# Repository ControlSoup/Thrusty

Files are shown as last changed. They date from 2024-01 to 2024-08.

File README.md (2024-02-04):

# How to Use

Assuming you have the required permissions to access this file. Here is how to clone and run the various projects in this file.

### Generate an ssh key

For a guide on how to generate an ssh key to clone this repo, see ->
[Github ssh keygen](https://docs.github.com/en/authentication/connecting-to-github-with-ssh/generating-a-new-ssh-key-and-adding-it-to-the-ssh-agent)

### Clone the repo

Use the ssh key on this repo and find a nice place in your file structure for it to be stored (Git folder, documents ect)

After you find that, open that path in a terminal.

Once your terminal is open, perform:
```bash
git clone [pasted ssh key form github]
```

### Install requirments and folder as a package

Once the repo is cloned, navigate to its file path, and perform the following command.

```
python3 -m pip install .
```

the "." denotes that you want to install the current folder (with setup.py)

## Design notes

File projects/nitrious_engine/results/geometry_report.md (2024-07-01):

==================== Geometry Report ====================
Chamber Area [in^2] = 5.94
Chamber Diameter [in] = 2.75
Chamber Length [in] = 6.0
Chamber Volume [in^3] = 37.38
Contraction Ratio [-] = 5.62
Exit Area [in^2] = 3.269
Exit Diameter [in] = 2.04
Exit Half Angle [rad] = 0.268
Exit Length [in] = 1.603
Expansion Ratio [-] = 3.093
Half Angle Losses [-] = 0.982
Lstar [in] = 35.37
Throat Area [in^2] = 1.057
Throat Diameter [in] = 1.16

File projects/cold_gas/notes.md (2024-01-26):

# Requirements:
- Model the thrust fluid conditions of a cold gas thruster
- Affordable at the hobby scale
- Model Supply requirements and run time for a given thruster setup
- Allow different gas storage parameters such as:
	- Fluid Medium
	- Pressure
	- Temperature
- Bonus Research Questions I want to answer:
	- Why Isentropic for choked flow conditions?
	- Can you make a vehicle that can fly for 5-10s from only cold gas propulsion?

# Sources:
- [Rocket Propulsion Elements #9](obsidian://open?vault=sattva&file=Papers%2FRocket%20Propulsion%2FTextbooks%2FRocket%20Propulsion%20Elements%209.pdf)

# Modeling Force!

Force in a nozzle is a product of the momentum of something exiting it. In the case of propulsion systems often these are very small particles of gas, at very high velocities. For a converging diverging nozzle I will use the following symbolic notation in the represented form:

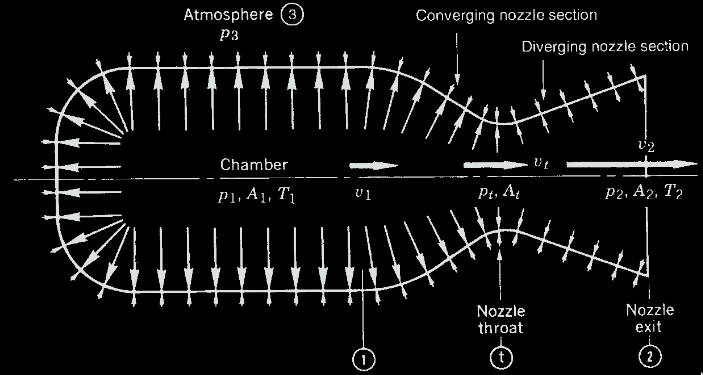
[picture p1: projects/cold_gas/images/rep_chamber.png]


The equation for thrust form the conditions through this system is :
$$\huge F = \dot{m}v_2 + (p_2-p_3)A_2$$

The derivation of this equation is from the Control Volume Approach from refs 2-3 and 2-4 in - [Rocket Propulsion Elements #9](obsidian://open?vault=sattva&file=Papers%2FRocket%20Propulsion%2FTextbooks%2FRocket%20Propulsion%20Elements%209.pdf).

The Chamber conditions are fairly easily defined from the source or tube attached to the system $p_1,A_1,T_1$. Seal Level atmospheric pressure is a great assumption for this project ($p_3$), so really... its just about finding the values for $\dot{m}$,  $v_2$ and $p_2$ given $A_2$.
##### Complete Thrust Equation

Note:
	the symbol $\kappa$ refers to a real gas constant, see : [[WIKI_Heat_capacity_ratio.pdf]]
	in some equations you will see $\gamma$ instead of $\kappa$

To capture the various gas effects going on, we need an equation that allows modification of the chamber geometry, working medium ect. The following equation can be used to perform trades on these various parameters.

Eq 3-29 from [Rocket Propulsion Elements #9](obsidian://open?vault=sattva&file=Papers%2FRocket%20Propulsion%2FTextbooks%2FRocket%20Propulsion%20Elements%209.pdf).
$$\huge F = A_tp_1\sqrt{\frac{2\kappa^2}{\kappa-1}\space\space\space\space(\frac{2}{\kappa+1})^\frac{\kappa+1}{\kappa-1}\space\space\space\space[1-\frac{p_2}{p_1}^\frac{\kappa-1}{\kappa}]} + (p_2 - p_3)A_2$$

This is an awesome equation for an initial design, however there will be need to be able to look at test data and directly compare with predictions. For this the thrust coefficient can be used.

##### Thrust Coefficient

These equations are essentially the same thing as the full thrust equation just shifting things around to make more direct comparisons with data.

Eq 3-30 from [Rocket Propulsion Elements #9](obsidian://open?vault=sattva&file=Papers%2FRocket%20Propulsion%2FTextbooks%2FRocket%20Propulsion%20Elements%209.pdf).
$$\huge C_F = \sqrt{\frac{2\kappa^2}{\kappa-1}\space\space\space\space(\frac{2}{\kappa+1})^\frac{\kappa+1}{\kappa-1}\space\space\space\space[1-\frac{p_2}{p_1}^\frac{\kappa-1}{\kappa}]} + \frac{A_2(p_2-p_3)}{A_tp_1} $$
and combining this with this full thrust equation gives us the final easy to compare formula for test data:

Eq 3-31 from [Rocket Propulsion Elements #9](obsidian://open?vault=sattva&file=Papers%2FRocket%20Propulsion%2FTextbooks%2FRocket%20Propulsion%20Elements%209.pdf)
$$\huge F = C_FA_tp_1$$
or for our use
$$\huge C_F = \frac{F}{A_tp_1}$$

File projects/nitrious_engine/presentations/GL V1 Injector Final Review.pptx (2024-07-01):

## Gaslighter V1 Engine FINAL REVIEW

Designer: Karl Kanmaz
Systems Engineer: Joe Wilson

## GL V1 Ideal System Specs

- Chamber Pressure = 150 psi
- Throat Diameter = 1.33 in
- Bulk Chamber Temp = 1937 F
- L* = 30 in
- MR = 1.6
- Area Ratio = 2.25
- Mass flow = 1.68 lbm/s
Max Thrust = 267.2 lbs

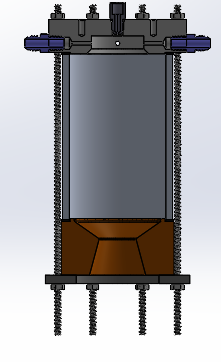
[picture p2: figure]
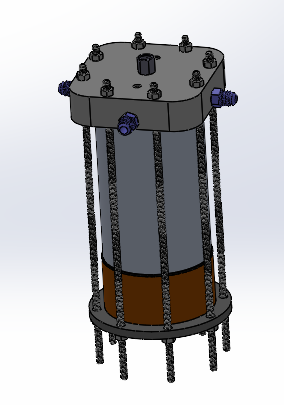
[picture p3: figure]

## Design

Injector
Material: 6061 Aluminum

Chamber
Material: 6061 T6 Tube
- Adjustable

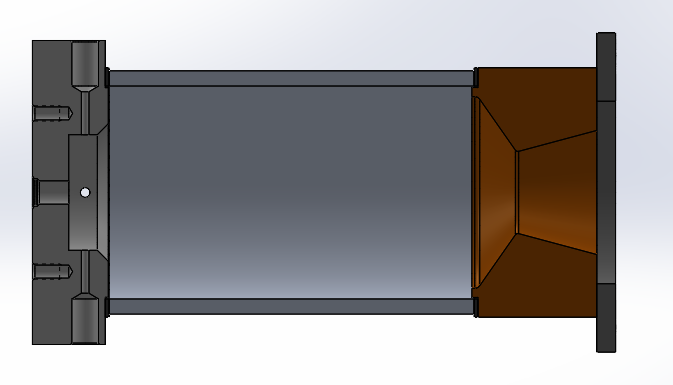
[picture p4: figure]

Clamp Plate
Material: Mild Steel

Graphite Gasket

Throat-Nozzle
Material: 360 Brass

## Pressure Ladder

Mdot_fuel = 0.65 lbm/s (0.29 kg/s)
V_tank = 0.011 m^3
Ullage % = 10%
Mass_fuel_max = 8 kg
Max Burn Time = 28 s

Injector Orifice 2X
Dp = 31.3 psi
P = 150 psi
⌀ 0.155”

Fuel Tank
187 psi

F-V-052

Injector

Chamber
150 psi

Outlet Pipe
Dp = 2.6 psi
P = 184.3 psi
Length = 4.9 ft
⌀ 0.44”
Relative Roughness= 0.0015

Branch Pipe 2X
Dp = 2.2 psi
P = 182.1 psi
Length = 10”
⌀ 0.375”
Roughness = …

Sump
Dp = 0
P = 187 psi
⌀ 0.5”
Cd = 0.65

Sump

Ball Valve - 052
Dp = 0.2 psi
P = 186.8 psi
Cv = 11.7

## Load - Cell Threads

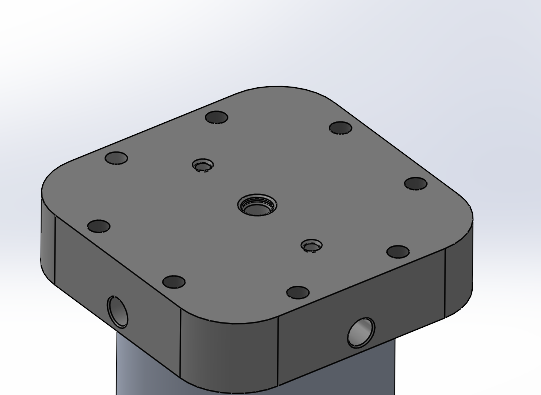
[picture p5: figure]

2X ¼” - 28 Thread
Length = 0.5”
Athread = PI*dm*Le / 3
Fsu = 30 ksi
FOS = 2
Pallowed = 2000 lbf (per thread)
- Aluminum threads may wear after many uses, be prepared to insert helicoil replacement

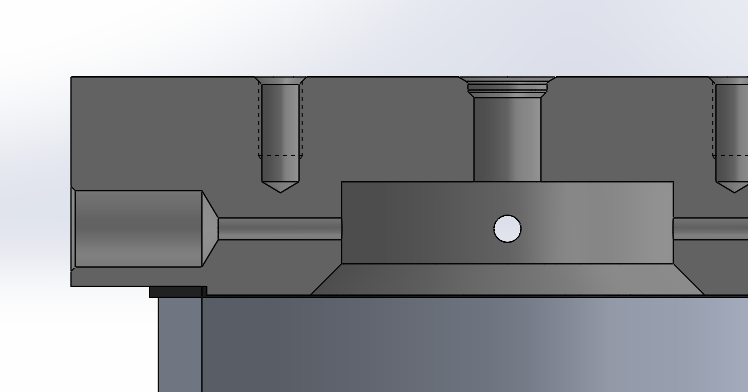
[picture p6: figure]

## Chamber Pressure Stress

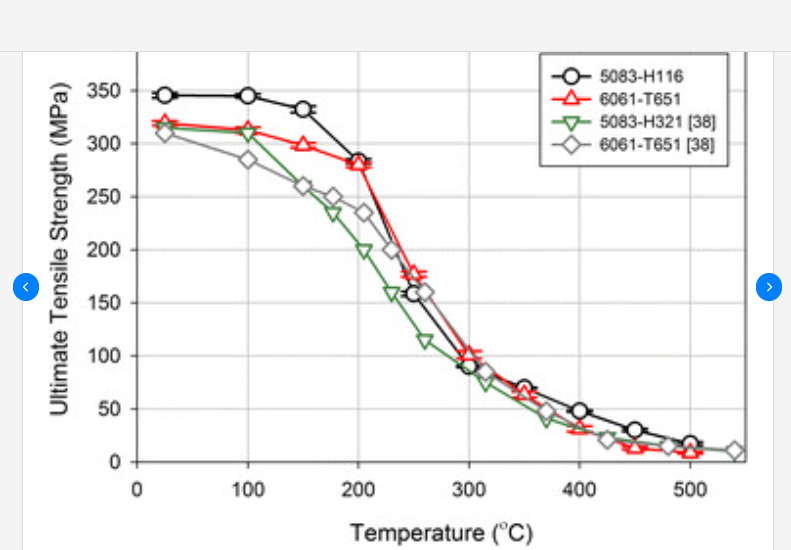
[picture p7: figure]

Hoop Stress = Pr/t
= (150 psi) * (1.75”) / (0.25”)
= 1050 psi [7 MPa]
- FOS_ult = 2
- Temp should be limited to approx. 400 Celsius ( 752 F)

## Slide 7

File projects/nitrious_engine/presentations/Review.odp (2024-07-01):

## Gaslighter V1 Engine FINAL REVIEW

Karl Kanmaz, Joe Wilson

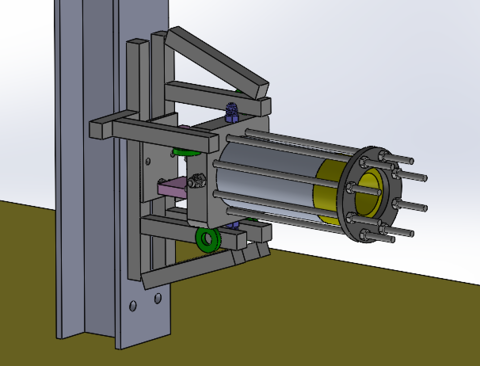
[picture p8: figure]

## Engine

- Chamber pressure chosen to keep fuel runtank < 200psia
- Engine mdot limited by fuel runtank pressures and volume (0.5gal/5s)
- Mixture ratio chosen to keep ideal chamber temps 10% over melting (1730F)
  - This is an conservative choise, based on combustion efficency expectations
  Design decisions on this motor are intended to provide
  an easy onramp to liquid propulsion instead of optimizing performance.

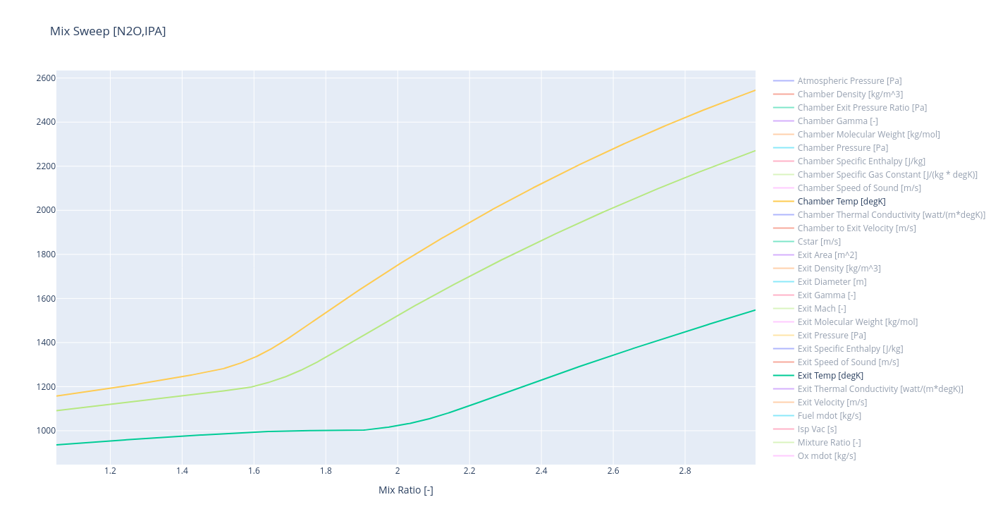
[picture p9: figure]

## Propellant

- Fuel: 99% Ipa
- Oxidizer: N2O (Automotive)
- Combustion properties from CEA
  Propellants chosen for their ease of use and avaliblity, at the cost of performance.
  Additional complexity is added by the use of a high vapor pressure oxidizer, this was perfered over the challanges of cryogenics for a small hobby project.

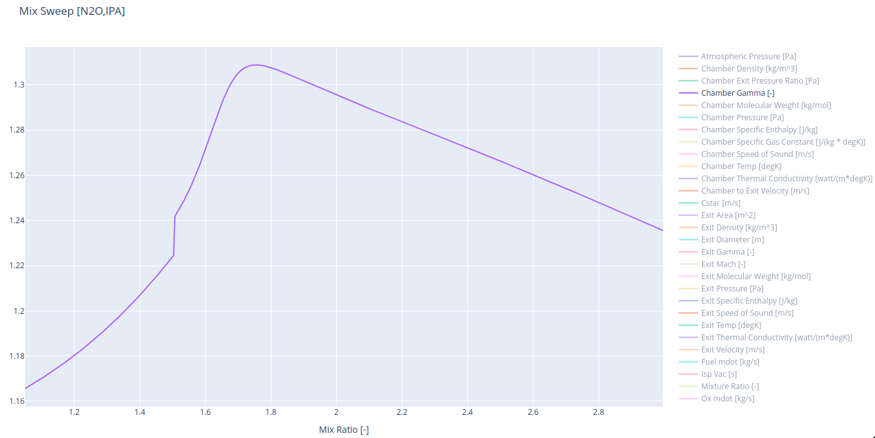
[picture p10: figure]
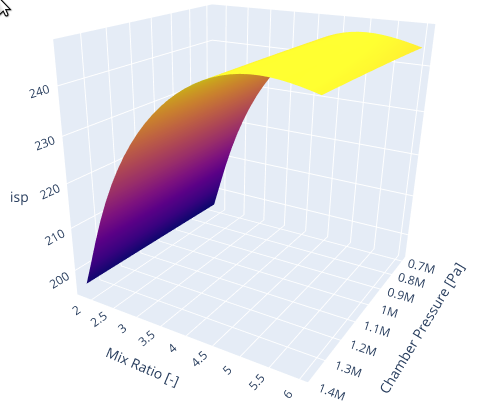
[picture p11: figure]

## GL V1 Ideal System Specs

- Chamber Pressure = 150 psi
- Throat Diameter = 1.33 in
- Bulk Chamber Temp = 1730 F
- L* = 30 in
- MR = 1.06
- Area Ratio = 2.25
- Mass flow = 1.68 lbm/s

Ideal Thrust = 267.2 lbs

## Design

Injector

Material: 6061 Aluminum

- Center OX orifice

- 2X fuel orifice (90 deg to OX orifice)

Chamber
Material: 6061 T6 Tube

ID: 2.75”

Length: 6”

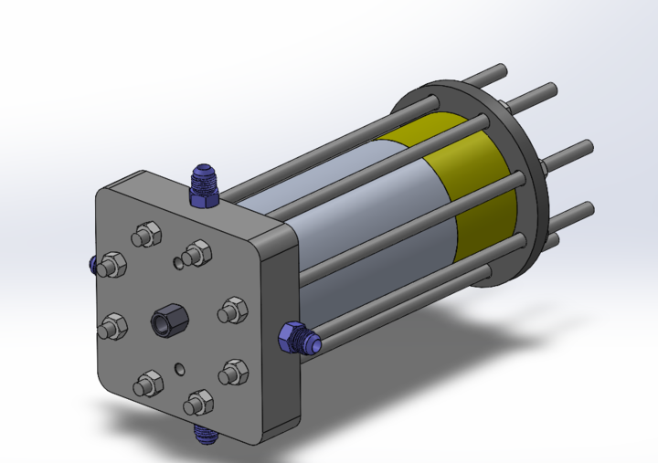
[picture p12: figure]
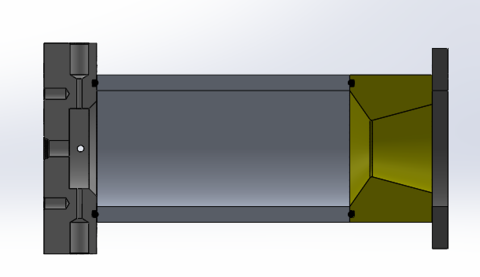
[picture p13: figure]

Clamp Plate

Material: Mild Steel

High Temp O-ring

Throat-Nozzle

Material: 360 Brass

## Heat Sink Modeling

- Assumes 100% Combustion Efficiency, and perfectly caloric products
- Throat temp = Chamber stagnation temperature
- Diffusivity chosen based by median flame temp (293K -> 1250K)
- Copper C360 (Brass) chosen to balance cost, melting temp and conductivity
- Heat transfer done with FDM discrete and rk4 integration

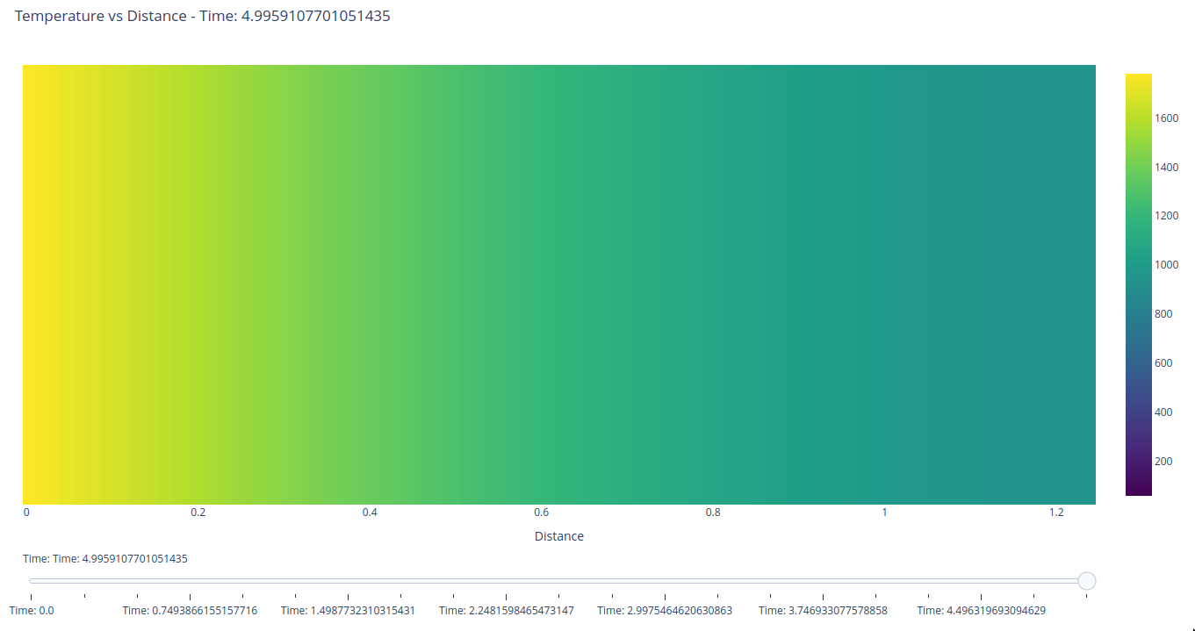
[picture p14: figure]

  780K Adiabatic Outer Wall Temp

Ambient Properties (https://www.matweb.com/search/DataSheet.aspx?MatGUID=bae961d2d6ed497a9096986641162def)

  Frontiers of Solidifcation (MPMD 2016)

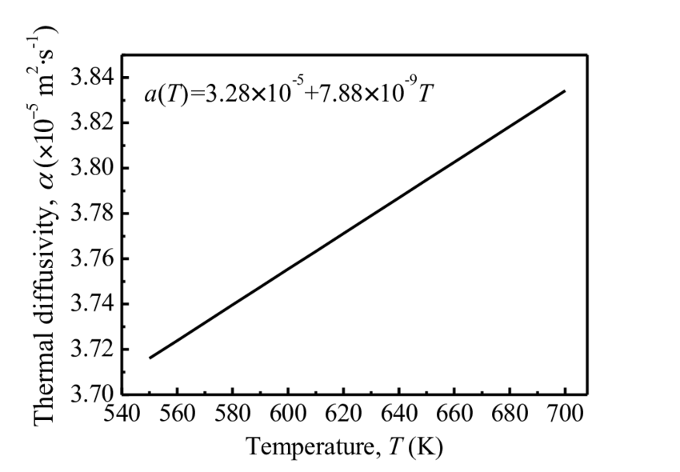
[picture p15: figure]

  Ambient Diffusivity (293K) = ~3.59e-5 [m2/s] Frontier Model Diffusivity(293K) = ~3.51e-5 [m2/s] Frontier Model Diffusivity(771K) = ~3.89e-5 [m2/s]
  Calc is likely conservative, but this demonstrates worst case conditions, and drives starting mixture ratio selection.
  Melting temp 1160K (0.141in)!

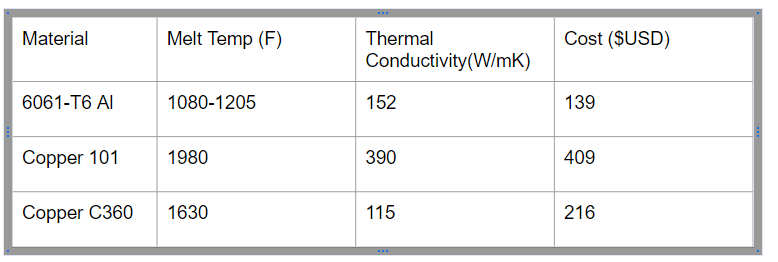
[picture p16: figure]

  1244K [FROM CEA]

## Throat Errosion

  Based on conservative heat sink modeling, throat erosion is likely.
  Effects of this:
  - Chamber pressure reduction
  - Exit Ratio decreases inverse with Exit Pressure and proportional to Exit velocity
  - Slight Chamber temperature reduction
  - Increased mdot from both injectors
  - For small erosion thrust increases, until exit velocity compromises mdot increase
  Risks:
  - Reduced injector stiffness (instability, or combustion gas up the feedline)
  - Loss of engine performance (lower isp, transition to under expansion and decreased exit velocity)
  Even with max expected errosion during a 5s burn, thrust loss is minimal. Injector stiffness risk will be accepted, and mitigated with an intial lower duration burn to access erosion

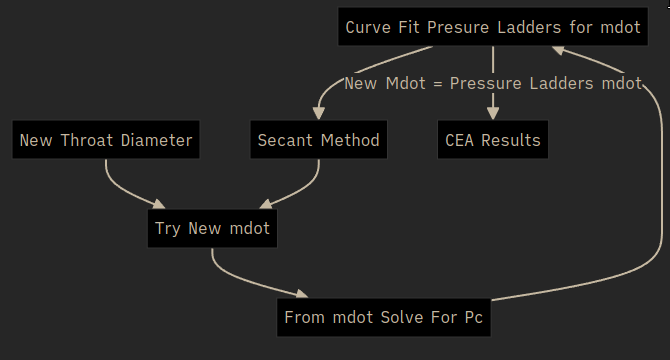
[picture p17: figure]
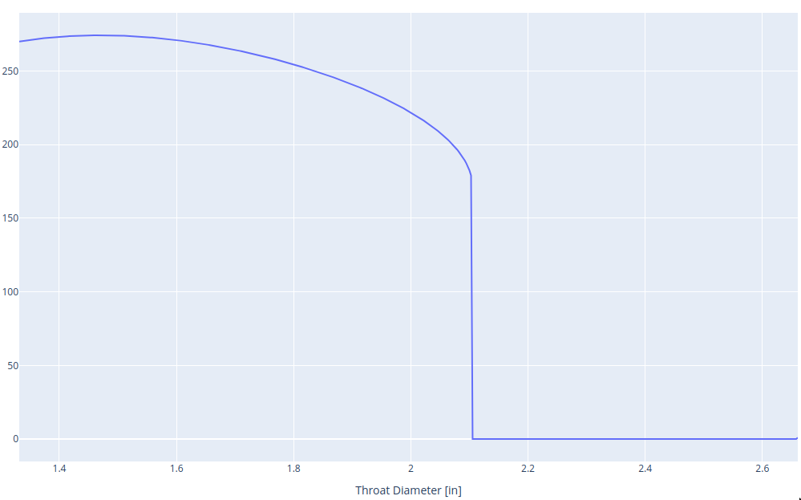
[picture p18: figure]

  Expansion = Unity
  Thrust

## Test P&ID / Instrumentation

  Risk Profile:
  - 2 Fault tolerant during manual operations
  - 1 Fault tolerant to loss of GSE
  - 0 Fault tolerant to engine loss
  Nitrous:
  - Nitrous outlet 20lbm + high flow siphon valve
  - Pressure / Temp at all major locations
  - Redundant purge checks to mitigate leakage flowing into fuel system if checked off
  - 4 x calibrated load cells to measure mass usage against injector mdot
  IPA:
  - IPA temperature considered ideally constant, only ullage pressure and injector fluid state are measured
  - 4 x calibrated load cells to measure mass usage against injector mdot
  Purge:
  - Limits moisture (from icing in Nos leakage or combustion products)
  - Acts as a small gas damper during startup (startup timing tbd)
  Chamber:
  - Chamber pt with thermal standoff
  - Chamber temperatures although low enough to measure with a K-type TC where not installed due to possibilities of increased chamber temps in the future
  - 3 x Skin temperature sensors on injector wall, chamber wall and throat location
  If budget allowed normally open valves , a remote pressurant isolation, and a separate volume for purge gas would have been desirable from a test stand perspective.

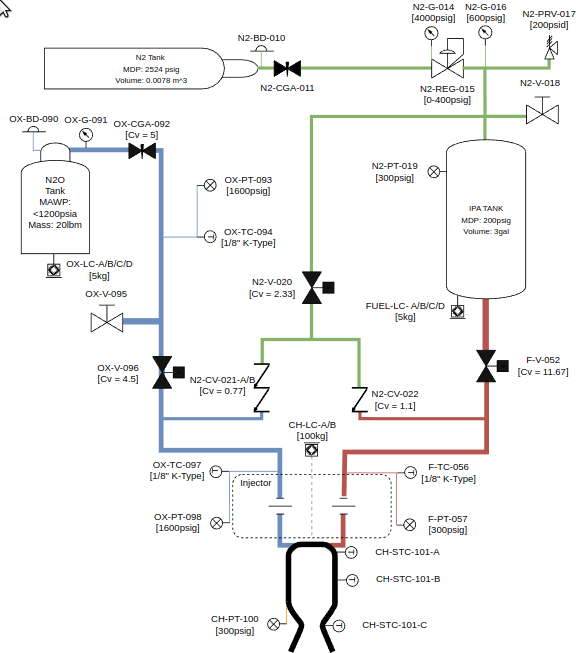
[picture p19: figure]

## Fuel Feed Pressure Ladder

Fuel Tank

187 psi

F-V-052

Injector

Chamber

150 psi

Mdot_fuel = 0.65 lbm/s (0.29 kg/s)

V_tank = 0.011 m^3

Ullage % = 10%

Mass_fuel_max = 8 kg

Max Burn Time = 28 s

Injector Orifice 2X

Dp = 31.3 psi

P = 150 psi

⌀ 0.155”

Branch Pipe 2X

Dp = 2.2 psi

P = 182.1 psi

Length = 10”

⌀ 0.375”

Roughness = …

Sump

Sump

Dp = 0

P = 187 psi

⌀ 0.5”

Cd = 0.65

Needle Valve - 052

Dp = 0.2 psi

P = 186.8 psi

Cv = 11.7

Outlet Pipe

Dp = 2.6 psi

P = 184.3 psi

Length = 4.9 ft

⌀ 0.44”

Relative Roughness= 0.0015

## Purge Sizing

- Control Mass Flow by choking upstream of feedlines this ensures down stream conditions do not effect purge mass flow-rate until critical conditions are met
- Ensure a minimum of 3 x volume exchanges based onNASA Lessons Learned (https://llis.nasa.gov/lesson/851) (For hydrogen but few sources exist for nitrous oxide / IPA)

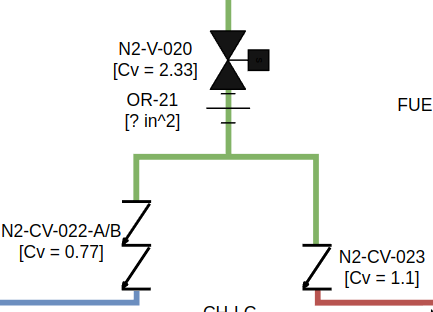
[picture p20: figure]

## Fuel Tank

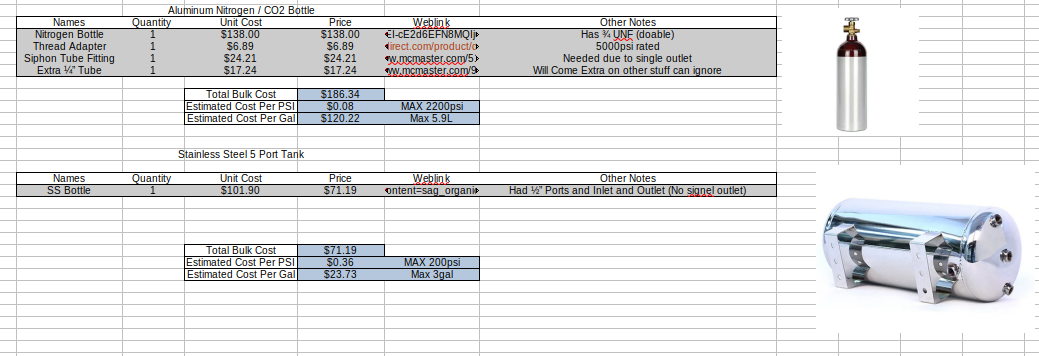
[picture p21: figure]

  Fuel Tank was chosen purley on cost and for lack of fabrication, for higher chamber pressures tapping the bottom of the nitrogen bottle, buying a 3/4” UNF fitting and proofing the assembly per B31.3 would be very cost effective

## DESIGN ANALYSIS

## Chamber Pressure Hoop Stress


Hoop Stress = Pr/t

= (150 psi) * (1.375”) / (0.375”)

= 550 psi [4 Mpa]

- Temp should be limited to approx. 400 Celsius (752 F) for chamber structural capability

## Seals

- O ring Diameter = 1/8” (0.139” Exact)
- O-ring maximum rated temperature = 450 F
  Pressure Separation Force = 1800 lbf
  Threaded Rods: 5/16” – 18 x 1 ft
  Joint Separation min. pre-load = 900 lbf
  Tie-rod min torque = 7.2 in-lbs

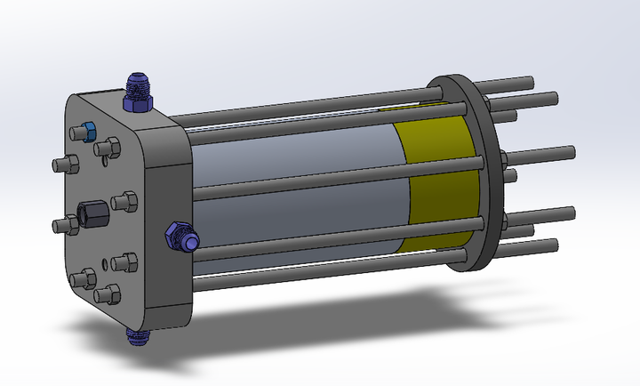
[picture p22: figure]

Separation Pressure

## Chamber Thermal Expansion

- Aluminum chamber will experience thermal expansion of 0.020” per every 100F heating
- Steel tie rods will experience same elongation and therefore increased tension during hot fire  Tie Rod Total Tension =

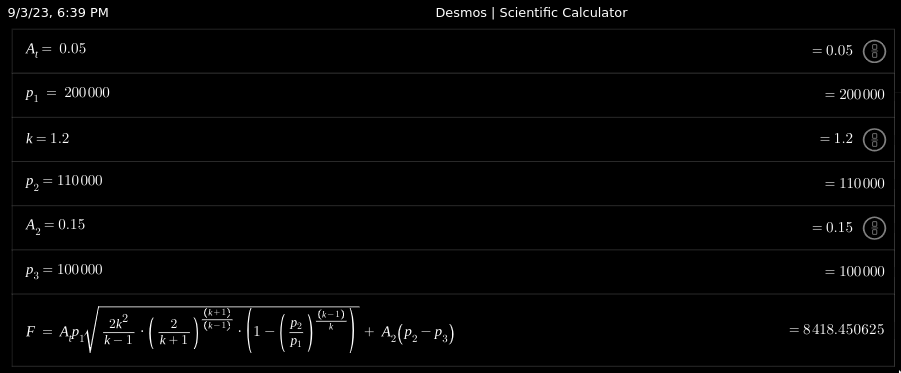
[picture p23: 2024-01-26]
projects/cold_gas/images/RPE_EQ-3-28_desmos.png

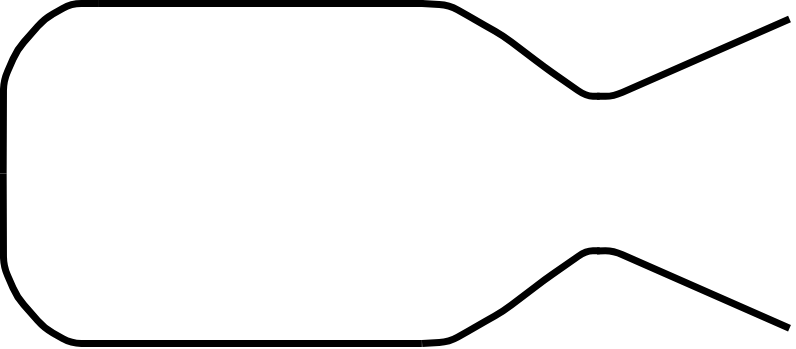
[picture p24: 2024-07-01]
projects/nitrious_engine/diagrams/engine.png

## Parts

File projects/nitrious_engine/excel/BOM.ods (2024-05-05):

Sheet: Global BOM
 |  | GSE BOM
Names | Quantity | Unit Cost | Price | Weblink | Other Notes | Ordered
Pressure Relief (300psig) | 2 | $29.74 | $59.48 | https://www.mcmaster.com/9889K19-9889K162/ | -
NOS Pts | 3 | $34.69 | $104.07 | https://www.amazon.com/FUSCH-Transducer-Connector-Stainless-Transmitter/dp/B0CRQT7VFJ | -
Fuel + Chamber Pts | 3 | $25.00 | $75.00 | https://www.amazon.com/Transducer-Stainless-Transmitter-Automobile-Motorcycle/dp/B09FXBHW9F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 | -
In Fluid Tcs | 3 | $30.44 | $91.32 | https://www.mcmaster.com/39095K64/ | -
TC Extension Wire | 1 | $28.94 | $28.94 | https://www.amazon.com/K-Type-Thermocouple-Wire-Solid-Insulation/dp/B074DKPJRL | -
Engine Load Cells | 2 | $25.00 | $50.00 | https://www.amazon.com/YZC-516C-Tension-Compression-Weight-batching/dp/B0BG9TH1S8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 | 100kg
N2 Regulator | 1 | $36.99 | $36.99 | https://www.amazon.com/Nitrogen-Regulator-Delivery-Pressure-Connection/dp/B09FXSDTFY | -
N2 Tank | 1 | $138.95 | $138.95 | https://www.amazon.com/Nitrogen-CGA580-Valve-Fresh-Certification/dp/B00CA31IMY | -
Fuel Tank | 1 | $127.00 | $127.00 | https://www.amazon.com/Kegco-I22-580-Nitrogen-Pressure-Aluminum/dp/B0037B3BLE | -
1000psi Valves | 3 | $17.26 | $51.78 | https://www.mcmaster.com/4112T23/ | -
Check Valves | 2 | $22.20 | $44.40 | https://www.mcmaster.com/7775K52/ | -
NOS Feed Valve | 1 | $109.98 | $109.98 | https://www.amazon.com/dp/B0CL6NX9V2/ref=twister_B0CL76SKJP?_encoding=UTF8&psc=1 | - | X
Purge Valve | 1 | $59.98 | $59.98 | https://www.amazon.com/U-S-Solid-Pressure-Solenoid-Valve/dp/B0BSNCWW34?hvadid=680323326402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 | -
Fuel Feed Valve | 1 | $84.98 | $84.98 | https://www.amazon.com/U-S-Solid-Pressure-Solenoid-Valve/dp/B0BSNHJ4WQ?hvadid=680323326402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 | -
NOS Tank | 1 | $495.97 | $495.97 | https://nitrousoutlet.com/cart | -
Fitting, Tube ect | 1 | $300.00 | $300.00 |  | Need to Add Detail
Tube Cutter | 1 | $15.99 | $15.99 | https://www.amazon.com/Libraton-Tubing-Deburring-Aluminum-Stainless/dp/B09J2JY1Q6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 | - | X
Tube Bender | 1 | $31.99 | $31.99 | https://www.amazon.com/VEVOR-Pipe-Tube-Bender-Manual/dp/B0C4F6BWDX | - | X
Tube Flare | 1 | $153.75 | $153.75 | https://www.aircraftspruce.com/catalog/topages/flaringtools2.php | - | X
Tank Load Cells | 8 | $1.75 | $13.98 | https://www.amazon.com/WWZMDiB-Amplifier-HX711-Displacement-Acceleration/dp/B0BLNQVY2X | 5kg
 |  | GSE Total | $2,074.55
 |  | Ignitor Bom
Names | Quantity | Unit Cost | Price | Weblink | Other Notes
Holder | 1 | $10.23 | $10.23 | https://www.mcmaster.com/9149K24/ | Thicker Wall for Snug Fit
Adapter | 1 | $6.28 | $6.28 | https://www.mcmaster.com/50785K614/ | -
Cap | 1 | $2.96 | $2.96 | https://www.mcmaster.com/50785K164/ | - |  | Total | $2,113.49
 | Ignitor Total | 2 | $38.94
 |  | DAQ
Names | Quantity | Unit Cost | Price | Weblink | Other Notes
TC Board | 1 | $52.95 | $52.95 | https://www.amazon.com/K-Type-Thermocouple-Breakout-MAX31855-200%C2%B0C/dp/B0B8B4CHDW?hvadid=652512145088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 | Comes With 8 Tcs
Power Supply | 1 | $23.99 | $23.99 | https://www.amazon.com/ALITOVE-Universal-Regulated-Switching-Transformer/dp/B078RTV9C4?hvadid=242168461154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 | 30A Max
Plug and Fuse | 1 | $10.00 | $10.00 | https://www.amazon.com/ASHATA-Rocker-Switch-Adapter-Printer/dp/B085VSS1F2?hvadid=647168045727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 | 15A Fuse
Valve Switches | 3 | $17.99 | $6.55 | https://www.tti.com/content/ttiinc/en/apps/part-detail.html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 | Spring Return Switches
ESTOP | 1 | $9.99 | $9.99 | https://www.amazon.com/Baomain-Emergency-Switch-Button-Weatherproof/dp/B00NTT91Y0 | STOP IT ALL
Diagnosis | 1 | $7.58 | $7.58 | https://www.amazon.com/Multimeter-Probe-Binding-Banana-Panel/dp/B0113IH0IW?hvadid=459486921002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 | Multi Meter Jacks
Cover Switches | 1 | $10.71 | $10.71 | https://www.amazon.com/Nilight-90014E-Rocker-Toggle-Warranty/dp/B07QKFD7Z7?hvadid=362768105905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 | Red Cover
TC Bulkheads | 4 | $6.50 | $25.98 | https://www.amazon.com/dp/B08BKTFJKX?s=industrial&sp_csd=d2lkZ2V0TmFtZT1zcF9kZXRhaWw | TC Bulkheads
 |  | COMS
Names | Quantity | Unit Cost | Price | Weblink | Other Notes
Walkie Talkie | 1 | 20.88 | 20.88 | https://www.amazon.com/Talkies-Two-Way-Channels-Flashlight-Survival/dp/B088H1BKDX | Lapels?

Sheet: Fuel Tank Trade
 |  |  |  |  |  | There is other options here, but I am avoiding welding or just tapping the cylinder (which would probably work)
 |  |  |  |  |  |  |  | Aluminum Nitrogen / CO2 Bottle
 |  |  |  |  |  | Names | Quantity | Unit Cost | Price | Weblink | Other Notes
 |  |  |  |  |  | Nitrogen Bottle | 1 | $127.00 | $127.00 | https://www.amazon.com/Kegco-I22-580-Nitrogen-Pressure-Aluminum/dp/B0037B3BLE | Has 1.125 UNF Thread :(
 |  |  |  |  |  | Thread Adapter | 1 | $124.00 | $124.00 | https://hydro-test.com/replacement-parts/100-056-adaptertest1-1-8brass/ | Extra 45 Dollars for 0.5” Outlet (NO PRESSURE RATING)
 |  |  |  |  |  | Siphon Tube Fitting | 1 | $24.21 | $24.21 | https://www.mcmaster.com/5182K113/ | Needed due to single outlet
 |  |  |  |  |  | Extra ¼” Tube | 1 | $17.24 | $17.24 | https://www.mcmaster.com/9924K11/ | Will Come Extra on other stuff can ignore most likley
 |  |  |  |  |  |  |  | Total Bulk Cost | $292.45
 |  |  |  |  |  |  |  | Estimated Cost Per PSI | $0.13 | MAX 2200psi
 |  |  |  |  |  |  |  | Estimated Cost Per Gal | $188.68 | Max 5.9L
 |  |  |  |  |  |  |  | Aluminum Nitrogen / CO2 Bottle
 |  |  |  |  |  | Names | Quantity | Unit Cost | Price | Weblink | Other Notes
 |  |  |  |  |  | Nitrogen Bottle | 1 | $138.00 | $138.00 | https://www.amazon.com/Nitrogen-CGA580-Valve-Fresh-Certification/dp/B00CA31IMY | Has ¾ UNF Thred :(
 |  |  |  |  |  | Thread Adapter | 1 | $6.89 | $6.89 | https://www.mscdirect.com/product/details/09107921 | 5000psi rated
 |  |  |  |  |  | Siphon Tube Fitting | 1 | $24.21 | $24.21 | https://www.mcmaster.com/5182K113/ | Needed due to single outlet
 |  |  |  |  |  | Extra ¼” Tube | 1 | $17.24 | $17.24 | https://www.mcmaster.com/9924K11/ | Will Come Extra on other stuff can ignore most likley
 |  |  |  |  |  |  |  | Total Bulk Cost | $186.34
 |  |  |  |  |  |  |  | Estimated Cost Per PSI | $0.08 | MAX 2200psi
 |  |  |  |  |  |  |  | Estimated Cost Per Gal | $120.22 | Max 5.9L
 |  | Random Tanks I Found
 |  |  |  |  |  |  |  | Stainless Steel 5 Port Tank
Material | Volume | Pressure | Cost | Weblink
AL | 2 Gal | 200psi | 199.95 | https://logiqair.com/products/50-10200 | - | Names | Quantity | Unit Cost | Price | Weblink | Other Notes
SS | 5 GAL | 300psi | ~250 | https://www.ebay.com/itm/186190526040?itmmeta=01HW9GJ2KGD15YP0M2T4MVP42B | - | SS Bottle | 1 | $101.90 | $71.19 | https://airbagit.com/products/upgrade-012?variant=44336747938066&currency=USD | Had ½” Ports and Inlet and Outlet (No signel outlet)
 |  |  |  |  |  |  |  | Total Bulk Cost | $71.19
 |  |  |  |  |  |  |  | Estimated Cost Per PSI | $0.36 | MAX 200psi
 |  |  |  |  |  |  |  | Estimated Cost Per Gal | $23.73 | Max 3gal

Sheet: State Measurment Trade
 |  | Aluminum Nitrogen / CO2 Bottle
Names | Quantity | Unit Cost | Price | Weblink | Other Notes
An Fitting and Guage Port | 2 | $13.94 | $27.88 | https://www.anplumbing.com/fuel-pressure-take-off-adapters-black-42871.html | https://www.anplumbing.com/fuel-pressure-take-off-adapters-black.html | -
Swage Adapter | 1 | $13.46 | $13.46 | https://www.mcmaster.com/5182K804/ |  |  | or
 |  | Total Per | $41.34
 |  | Aluminum Nitrogen / CO2 Bottle
Names | Quantity | Unit Cost | Price | Weblink | Other Notes
Male AN Fitting | 1 | $13.94 | $13.94 | https://www.anplumbing.com/fuel-pressure-take-off-adapters-black-42871.html
Female An fitting | 1 | $15.15 | $15.15 | https://www.anplumbing.com/straight-a-n-female-swivel-to-male-npt-31076.html
NPT Cross | 1 | 29.21 | 29.21 | https://www.mcmaster.com/50785K235/
Swage 1/8” probe ¼” npt | 1 | $15.66 | $15.66 | https://www.mcmaster.com/5182K405
 |  | Total Per | $73.96
 |  |  |  |  | https://www.anplumbing.com/straight-a-n-female-swivel-to-male-npt-31076.html

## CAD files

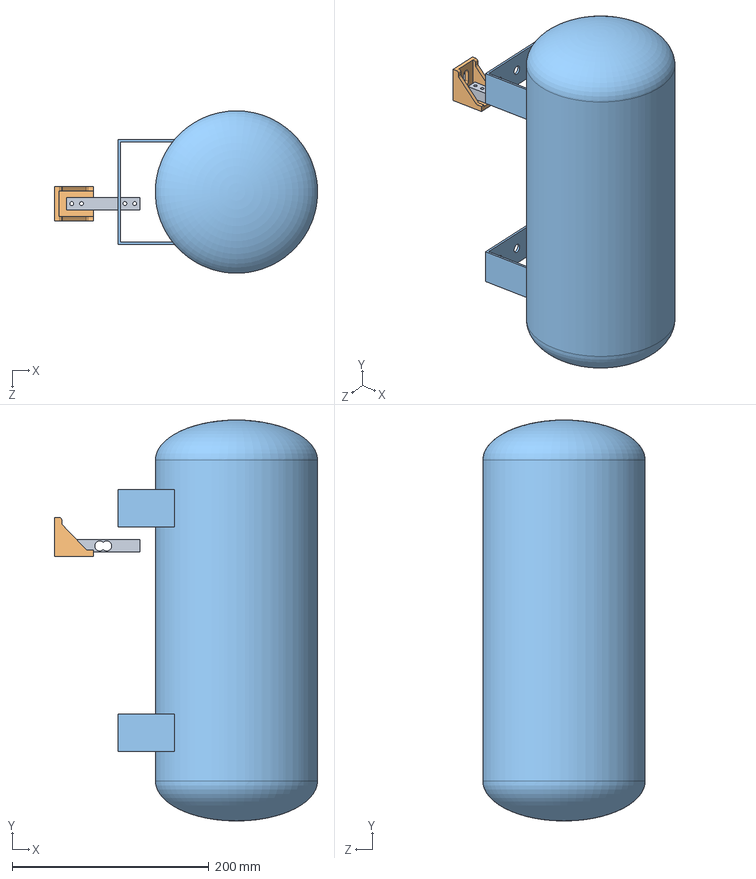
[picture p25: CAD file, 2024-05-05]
projects/nitrious_engine/CAD/Assemblies/FuelTankStructure.SLDASM
267.6 x 407.7 x 165.1 mm
AIRBAGIT_3GALLON_5PORT_OML
4040_20mm_slot_corner
ShanHJLoadCell

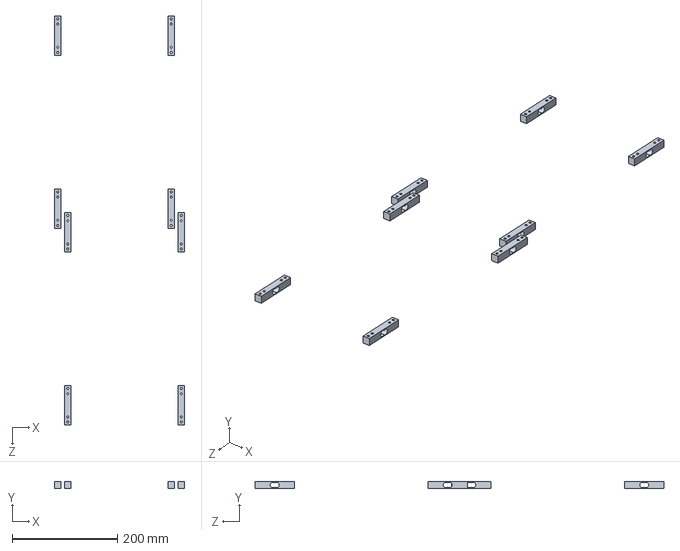
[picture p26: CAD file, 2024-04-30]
projects/nitrious_engine/CAD/Assemblies/BottleScale.SLDASM
247.6 x 12.7 x 777.8 mm
ShanHJLoadCell x 8

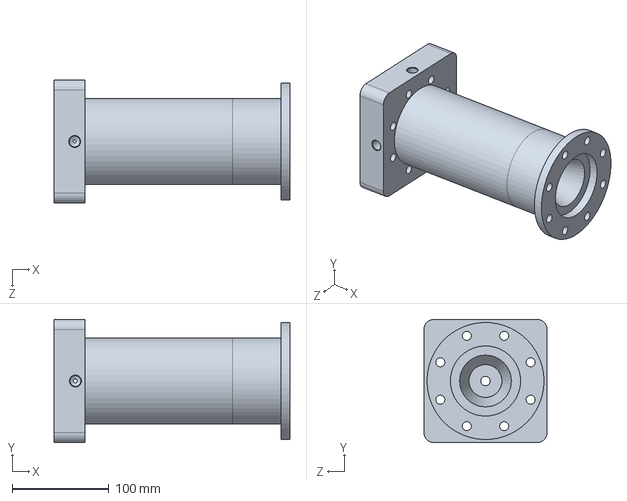
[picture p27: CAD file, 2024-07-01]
projects/nitrious_engine/CAD/Chamber/TCA V18.SLDPRT
243.4 x 127.0 x 127.0 mm

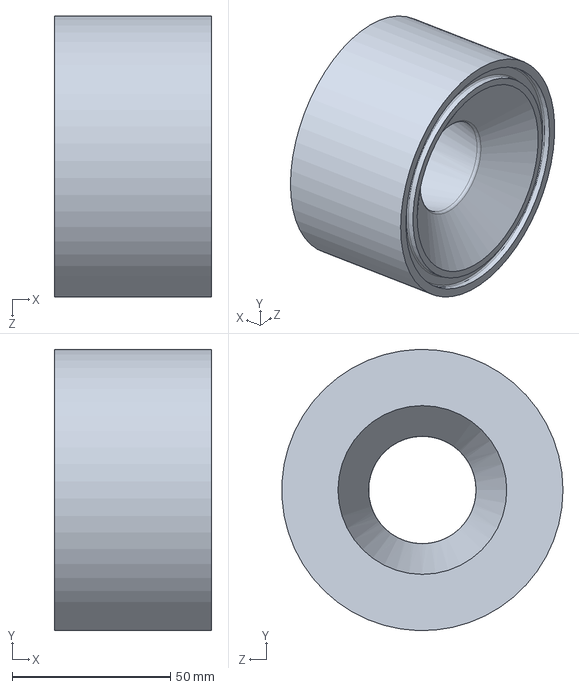
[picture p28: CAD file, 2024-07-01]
projects/nitrious_engine/CAD/Exports/Nozzle V11.SLDPRT
49.7 x 88.9 x 88.8 mm

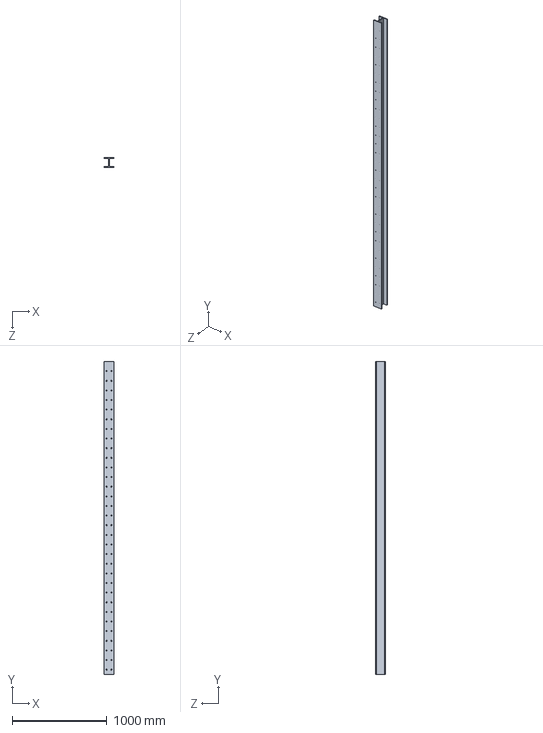
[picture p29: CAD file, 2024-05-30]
projects/nitrious_engine/CAD/FAR/Small I beam.SLDPRT
101.6 x 3302.0 x 101.6 mm

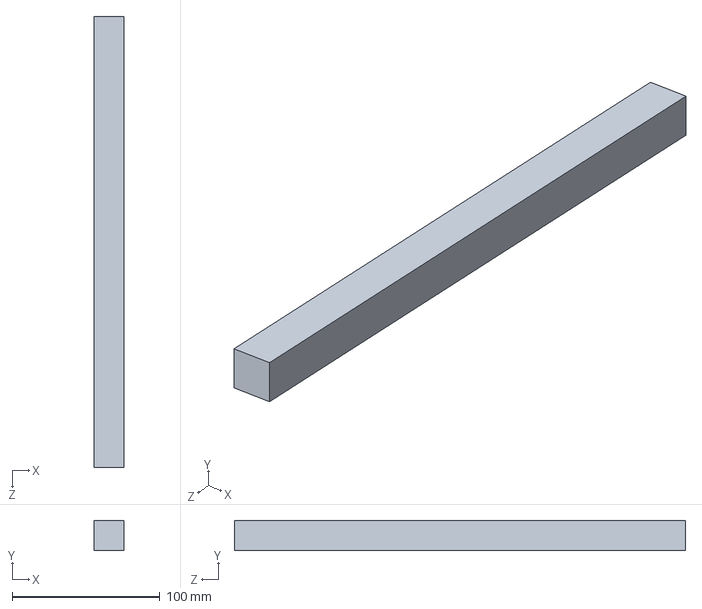
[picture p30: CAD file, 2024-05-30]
projects/nitrious_engine/CAD/Frame/2020 Framing, 1 ft.SLDPRT
20.3 x 20.3 x 304.8 mm

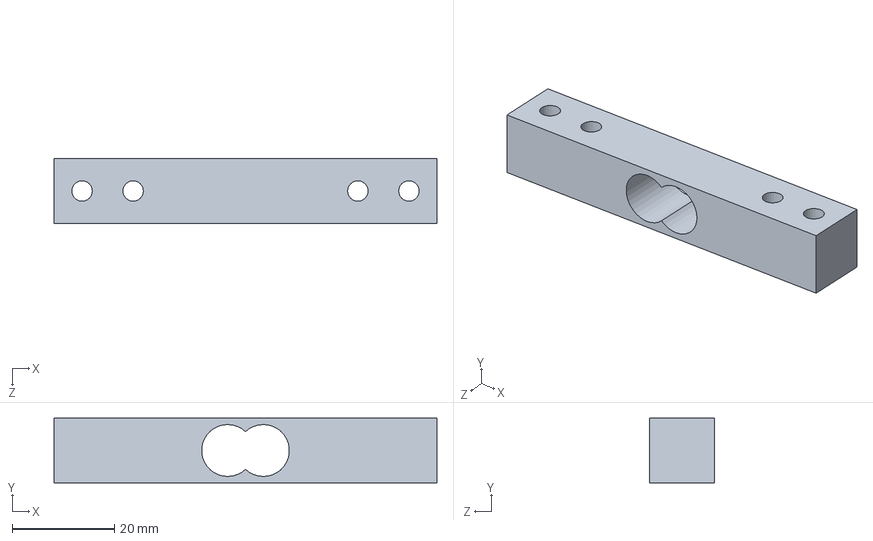
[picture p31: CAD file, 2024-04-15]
projects/nitrious_engine/CAD/Instrumentation/ShanHJLoadCell.SLDPRT
75.0 x 12.7 x 12.7 mm

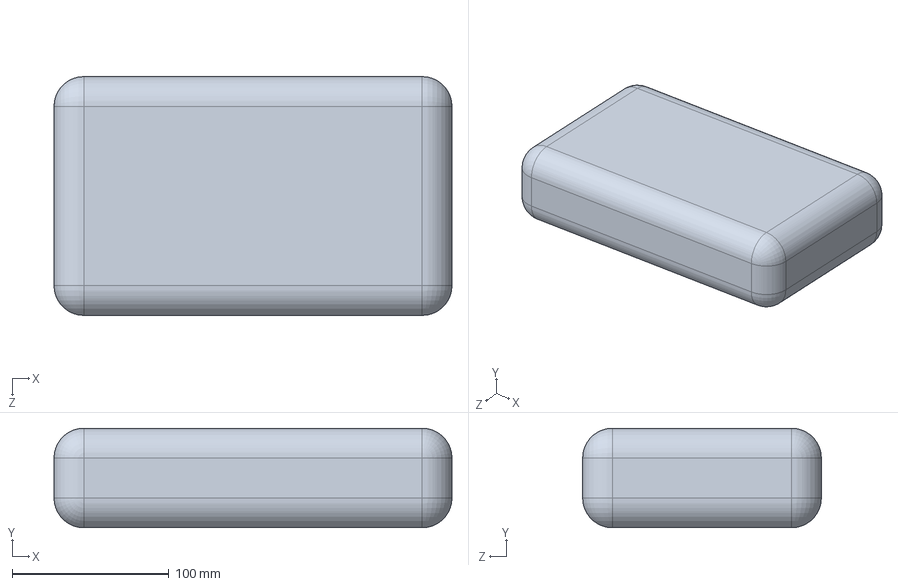
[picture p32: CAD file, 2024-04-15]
projects/nitrious_engine/CAD/Misc/Sandbag.SLDPRT
254.0 x 63.5 x 152.4 mm

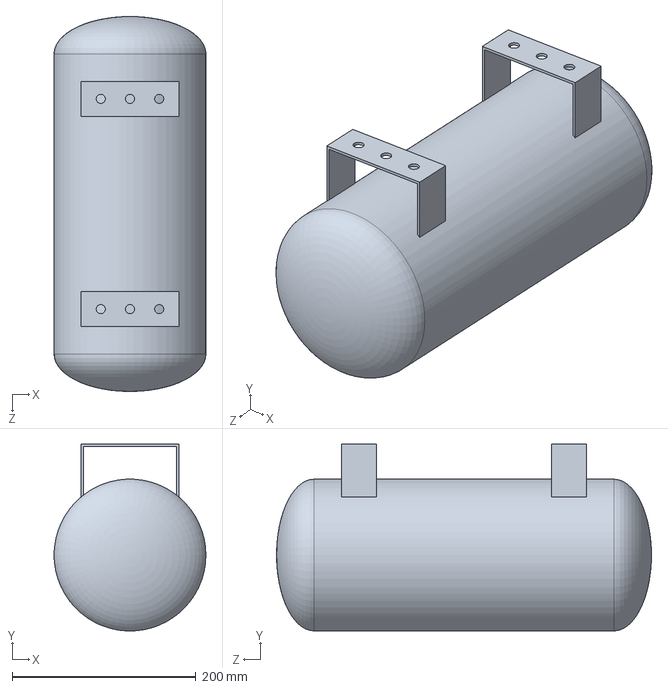
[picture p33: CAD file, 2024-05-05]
projects/nitrious_engine/CAD/Tanks/Fuel/AIRBAGIT_3GALLON_5PORT_OML.SLDPRT
165.1 x 203.1 x 407.7 mm

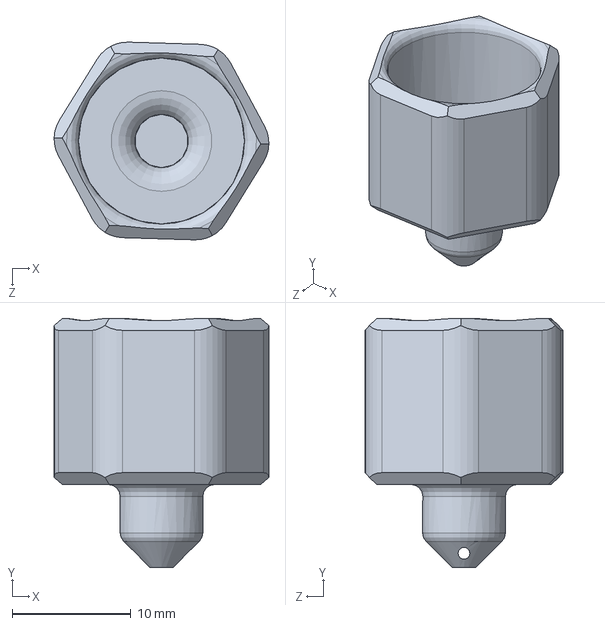
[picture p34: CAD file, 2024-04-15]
projects/nitrious_engine/CAD/Tanks/N2O/Bouchon.SLDPRT
18.1 x 21.0 x 16.7 mm

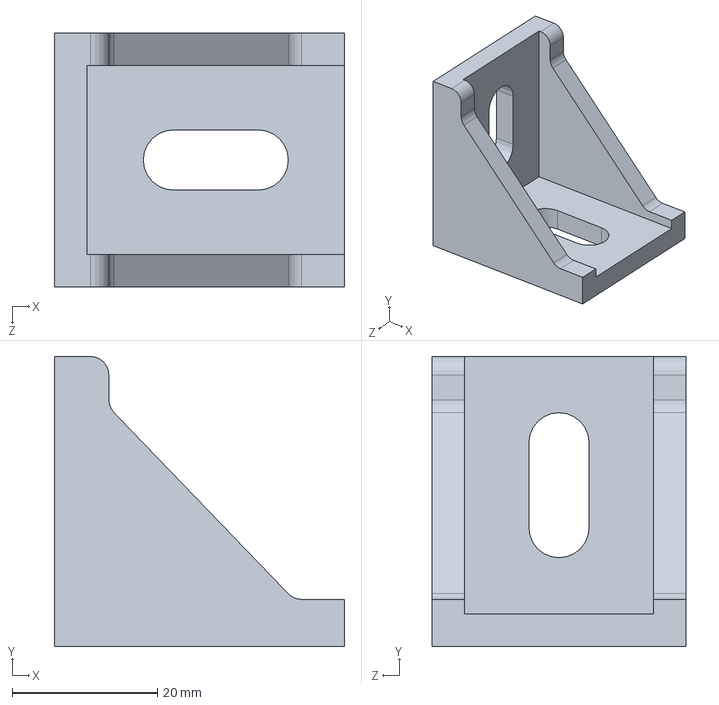
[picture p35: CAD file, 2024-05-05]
projects/nitrious_engine/CAD/Brackets/4040_20mm_slot_corner.SLDPRT
40.0 x 40.0 x 35.0 mm

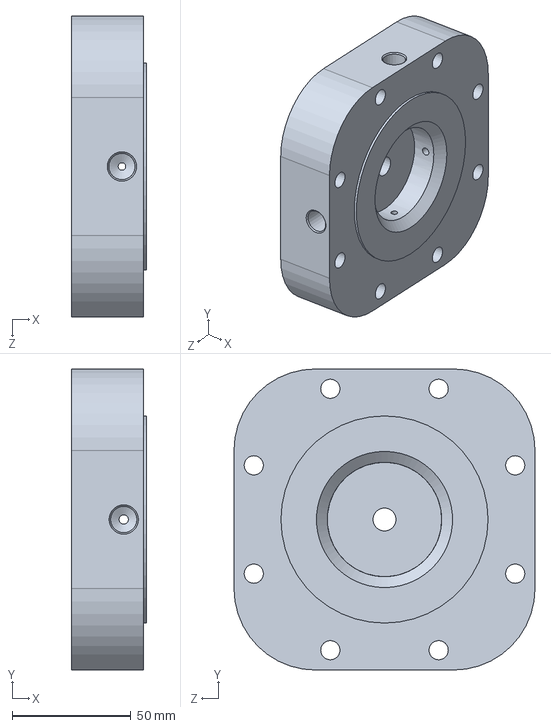
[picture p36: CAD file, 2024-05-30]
projects/nitrious_engine/CAD/Exports/Injector V8.SLDPRT
31.8 x 127.0 x 127.0 mm

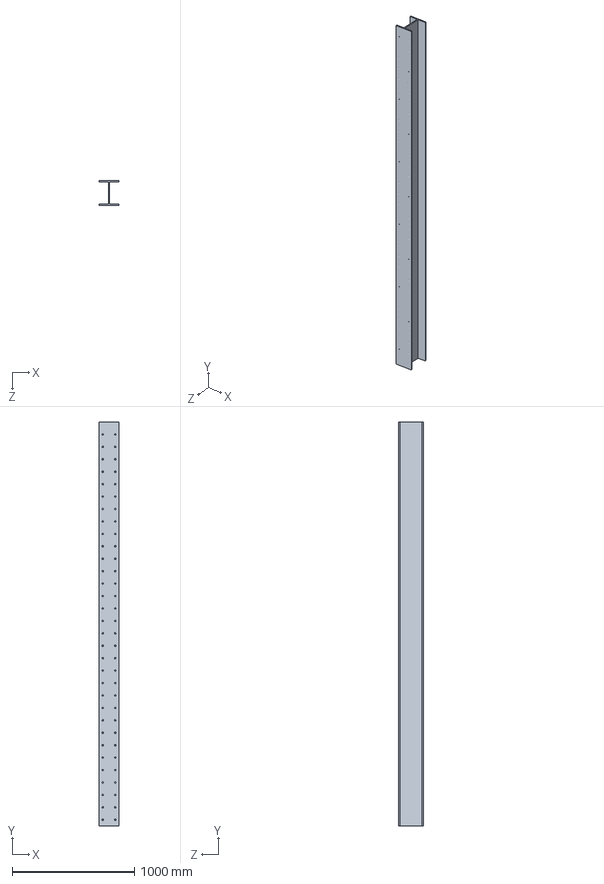
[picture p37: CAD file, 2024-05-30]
projects/nitrious_engine/CAD/FAR/Big I Beam.SLDPRT
165.1 x 3302.0 x 203.2 mm

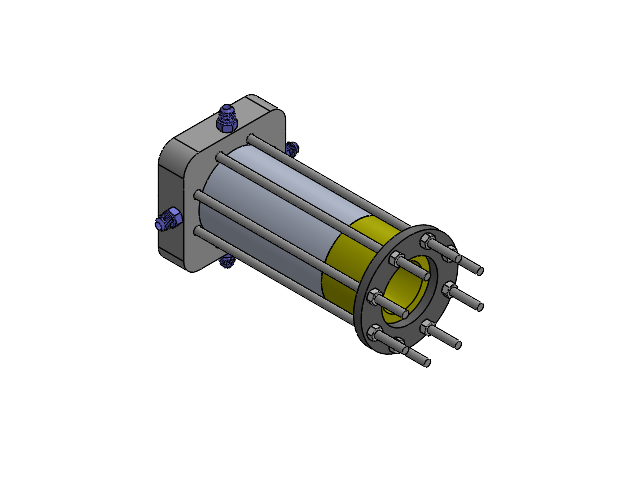
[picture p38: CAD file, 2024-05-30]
projects/nitrious_engine/CAD/Assemblies/TC Ass1.SLDASM
TCA V17
3313N143_High-Strength Steel Threaded Rod x 8
94895A810_High-Strength Steel Hex Nut x 16
50715K163_37 Degree Flared Fitting for Stainless Steel Tubing x 4
cfj4-60-ss-o'keefecontrolsco.-3d-03-30-2024

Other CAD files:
projects/nitrious_engine/CAD/Assemblies/Engine V4 -Hz.SLDASM
projects/nitrious_engine/CAD/Assemblies/Engine V2.SLDASM
projects/nitrious_engine/CAD/Assemblies/Engine V3 (Horizontal).SLDASM
projects/nitrious_engine/CAD/Assemblies/FeedSystem.SLDASM
projects/nitrious_engine/CAD/Assemblies/TCA V1.SLDPRT
projects/nitrious_engine/CAD/Brackets/3136N148_T-Slotted Framing.SLDPRT
projects/nitrious_engine/CAD/Chamber/ChamberV1.SLDPRT
projects/nitrious_engine/CAD/Chamber/TCA V12.SLDPRT
projects/nitrious_engine/CAD/Chamber/TCA V13.SLDPRT
projects/nitrious_engine/CAD/Chamber/TCA V14.SLDPRT
projects/nitrious_engine/CAD/Chamber/TCA V15.SLDPRT
projects/nitrious_engine/CAD/Chamber/TCA V16.SLDPRT
projects/nitrious_engine/CAD/Chamber/TCA V17.SLDPRT
projects/nitrious_engine/CAD/Exports/Drawings/Injector V2.SLDDRW
projects/nitrious_engine/CAD/Exports/Drawings/Injector V6.SLDDRW
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

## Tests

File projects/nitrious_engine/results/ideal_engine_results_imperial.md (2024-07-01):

==================== Current Engine Results ====================
Chamber Density [lbm/in^3] = 6.363e-05
Chamber Exit Pressure Ratio [-] = 10.69557502
Chamber Gamma [-] = 1.19214433
Chamber Molecular Weight [lbm/mol] = 0.03799417
Chamber Pressure [psia] = 150.0
Chamber Specific Enthalpy [ft*lbf/lbm] = -310350.12923988
Chamber Specific Gas Constant [ft*lbf/(lbm * degF)] = 83.17367654
Chamber Speed of Sound [in/s] = 32939.94905724
Chamber Temp [degF] = 1731.14464501
Chamber Thermal Conductivity [Btu/(hr*ft*degF)] = 0.22826703
Chamber to Exit Velocity [in/s] = 60524.02944775
Cstar [in/s] = 46813.77378959
Eps [-] = 2.5
Exit Area [in^2] = 3.4701105
Exit Density [lbm/in^3] = 8.18e-06
Exit Diameter [in] = 2.10197096
Exit Gamma [-] = 1.13125815
Exit Mach [-] = 2.21119924
Exit Molecular Weight [lbm/mol] = 0.04096136
Exit Pressure [psia] = 14.02449141
Exit Specific Enthalpy [ft*lbf/lbm] = -705678.03076182
Exit Speed of Sound [in/s] = 27371.49260804
Exit Temp [degF] = 1258.95561352
Exit Thermal Conductivity [Btu/(hr*ft*degF)] = 0.29586647
Exit Velocity [in/s] = 60523.82364289
Fuel mdot [lbm/s] = 0.74712727
Isp Vac [s] = 185.10349149
Isp Sutton [s] = 156.76149557
Mixture Ratio [-] = 1.2983347
Ox mdot [lbm/s] = 0.97002126
Throat Area [in^2] = 1.3880442
Throat Density [lbm/in^3] = 3.957e-05
Throat Diameter [in] = 1.32940316
Throat Gamma [-] = 1.16983634
Throat Molecular Weight [lbm/mol] = 0.03867201
Throat Specific Enthalpy [ft*lbf/lbm] = -415822.4900829
Throat Specific Gas Constant [ft*lbf/(lbm * degF)] = 89.66920409
Throat Speed of Sound [in/s] = 31261.96734691
Throat Temp [degF] = 1587.13223498
Throat Thermal Conductivity [Btu/(hr*ft*degF)] = 0.25137595
Throat Velocity [in/s] = 31261.96734691
Throat to Exit Velocity [in/s] = 51825.0707396
Thrust Ideal [lbf] = 269.18277129
Mdot [lbm/s] = 1.71714853
Critical pressure [psia] = 84.90092168

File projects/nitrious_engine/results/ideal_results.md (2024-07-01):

==================== Ideal Engine Results ====================
Chamber Density [kg/m^3] = 1.76125194
Chamber Exit Pressure Ratio [-] = 10.69557502
Chamber Gamma [-] = 1.19214433
Chamber Molecular Weight [kg/mol] = 0.01723387
Chamber Pressure [Pa] = 1034213.59397525
Chamber Specific Enthalpy [J/kg] = -927657.30492865
Chamber Specific Gas Constant [J/(kg * degK)] = 447.5010333
Chamber Speed of Sound [m/s] = 836.67470605
Chamber Temp [degK] = 1217.11924723
Chamber Thermal Conductivity [watt/(m*degK)] = 0.39506973
Chamber to Exit Velocity [m/s] = 1537.31034797
Cstar [m/s] = 1189.06985426
Eps [-] = 2.5
Exit Area [m^2] = 0.00223878
Exit Density [kg/m^3] = 0.22630759
Exit Diameter [m] = 0.05339006
Exit Gamma [-] = 1.13125815
Exit Mach [-] = 2.21119924
Exit Molecular Weight [kg/mol] = 0.01857976
Exit Pressure [Pa] = 96695.46440248
Exit Specific Enthalpy [J/kg] = -2109318.8579209
Exit Speed of Sound [m/s] = 695.23591224
Exit Temp [degK] = 954.79200751
Exit Thermal Conductivity [watt/(m*degK)] = 0.51206642
Exit Velocity [m/s] = 1537.30512053
Fuel mdot [kg/s] = 0.33889123
Isp Vac [s] = 185.10349149
Isp Sutton [s] = 156.76149557
Mixture Ratio [-] = 1.2983347
Ox mdot [kg/s] = 0.43999424
Throat Area [m^2] = 0.00089551
Throat Density [kg/m^3] = 1.09533894
Throat Diameter [m] = 0.03376684
Throat Gamma [-] = 1.16983634
Throat Molecular Weight [kg/mol] = 0.01754133
Throat Specific Enthalpy [J/kg] = -1242921.24969883
Throat Specific Gas Constant [J/(kg * degK)] = 482.44905305
Throat Speed of Sound [m/s] = 794.05397061
Throat Temp [degK] = 1137.11235277
Throat Thermal Conductivity [watt/(m*degK)] = 0.43506514
Throat Velocity [m/s] = 794.05397061
Throat to Exit Velocity [m/s] = 1316.35679679
Thrust Ideal [N] = 1197.38462171
Mdot [kg/s] = 0.77888547
Critical pressure [Pa] = 585371.24897269

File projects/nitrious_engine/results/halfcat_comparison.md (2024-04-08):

==================== Halfcat Comparision ====================
Chamber Area [m^2] = 0.002
Chamber Density [kg/m^3] = 1.898
Chamber Diameter [m] = 0.051
Chamber Exit Pressure Ratio [-] = 26.902
Chamber Gamma [-] = 1.262
Chamber Length [m] = 0.127
Chamber Molecular Weight [kg/mol] = 0.021
Chamber Pressure [Pa] = 1758163.11
Chamber Specific Enthalpy [J/kg] = 79346.496
Chamber Specific Gas Constant [J/(kg * degK)] = 405.101
Chamber Speed of Sound [m/s] = 1081.29
Chamber Temp [degK] = 2285.081
Chamber Thermal Conductivity [watt/(m*degK)] = 0.275
Chamber Volume [m^3] = 0.0
Chamber to Exit Velocity [m/s] = 2090.039
Contraction Ratio [-] = 4.0
Cstar [m/s] = 1455.28
Exit Area [m^2] = 0.002
Exit Density [kg/m^3] = 0.145
Exit Diameter [m] = 0.051
Exit Gamma [-] = 1.28
Exit Half Angle [rad] = 0.349
Exit Length [m] = 0.035
Exit Mach [-] = 2.747
Exit Molecular Weight [kg/mol] = 0.021
Exit Pressure [Pa] = 65354.177
Exit Specific Enthalpy [J/kg] = -2104785.421
Exit Speed of Sound [m/s] = 760.811
Exit Temp [degK] = 1116.374
Exit Thermal Conductivity [watt/(m*degK)] = 0.146
Exit Velocity [m/s] = 2090.032
Expansion Ratio [-] = 4.0
Fuel mdot [kg/s] = 0.245
Half Angle Losses [-] = 0.97
Isp Vac [s] = 235.189
Lstar [m] = 0.513
Mdot [kg/s] = 0.883
Mixture Ratio [-] = 2.605
Ox mdot [kg/s] = 0.638
Throat Area [m^2] = 0.001
Throat Density [kg/m^3] = 1.185
Throat Diameter [m] = 0.025
Throat Gamma [-] = 1.272
Throat Molecular Weight [kg/mol] = 0.021
Throat Specific Enthalpy [J/kg] = -440039.03
Throat Specific Gas Constant [J/(kg * degK)] = 405.387
Throat Speed of Sound [m/s] = 1019.212
Throat Temp [degK] = 2015.862
Throat Thermal Conductivity [watt/(m*degK)] = 0.229
Throat Velocity [m/s] = 1019.212
Throat to Exit Velocity [m/s] = 1824.69
Thrust Efficency Fraction [-] = 0.679
Thrust Ideal [N] = 1845.498
Thrust With Losses [N] = 1252.895

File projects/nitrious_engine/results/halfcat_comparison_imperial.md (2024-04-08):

==================== Halfcat Comparision Imperial ====================
Chamber Area [in^2] = 3.142
Chamber Density [lbm/in^3] = 0.0
Chamber Diameter [in] = 2.0
Chamber Exit Pressure Ratio [-] = 26.902
Chamber Gamma [-] = 1.262
Chamber Length [in] = 5.0
Chamber Molecular Weight [lbm/mol] = 0.045
Chamber Pressure [psia] = 255.0
Chamber Specific Enthalpy [ft*lbf/lbm] = 26545.573
Chamber Specific Gas Constant [ft*lbf/(lbm * degF)] = 75.293
Chamber Speed of Sound [in/s] = 42570.468
Chamber Temp [degF] = 3653.475
Chamber Thermal Conductivity [Btu/(hr*ft*degF)] = 0.159
Chamber Volume [in^3] = 15.866
Chamber to Exit Velocity [in/s] = 82285.008
Contraction Ratio [-] = 4.0
Cstar [in/s] = 57294.498
Exit Area [in^2] = 3.142
Exit Density [lbm/in^3] = 0.0
Exit Diameter [in] = 2.0
Exit Gamma [-] = 1.28
Exit Half Angle [rad] = 0.349
Exit Length [in] = 1.374
Exit Mach [-] = 2.747
Exit Molecular Weight [lbm/mol] = 0.045
Exit Pressure [psia] = 9.479
Exit Specific Enthalpy [ft*lbf/lbm] = -704161.358
Exit Speed of Sound [in/s] = 29953.176
Exit Temp [degF] = 1549.803
Exit Thermal Conductivity [Btu/(hr*ft*degF)] = 0.085
Exit Velocity [in/s] = 82284.728
Expansion Ratio [-] = 4.0
Fuel mdot [lbm/s] = 0.54
Half Angle Losses [-] = 0.97
Isp Vac [s] = 235.189
Lstar [in] = 20.201
Mdot [lbm/s] = 1.947
Mixture Ratio [-] = 2.605
Ox mdot [lbm/s] = 1.407
Throat Area [in^2] = 0.785
Throat Density [lbm/in^3] = 0.0
Throat Diameter [in] = 1.0
Throat Gamma [-] = 1.272
Throat Molecular Weight [lbm/mol] = 0.045
Throat Specific Enthalpy [ft*lbf/lbm] = -147216.185
Throat Specific Gas Constant [ft*lbf/(lbm * degF)] = 75.346
Throat Speed of Sound [in/s] = 40126.452
Throat Temp [degF] = 3168.881
Throat Thermal Conductivity [Btu/(hr*ft*degF)] = 0.133
Throat Velocity [in/s] = 40126.452
Throat to Exit Velocity [in/s] = 71838.18
Thrust Efficency Fraction [-] = 0.679
Thrust Ideal [lbf] = 414.885
Thrust With Losses [lbf] = 281.662

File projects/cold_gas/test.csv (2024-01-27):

mdot [kg/s] | udot [J/s] | tank.mass [kg] | tank.volume [kg] | tank.inenergy [J] | tank.pressure [Pa] | tank.temperature [K] | tank.density [kg/m^3] | tank.sp_inenergy [J/kg] | tank.sp_enthalpy [J/kg] | time [s]
-0.09 | -37013.89303644299 | 0.0633542878175454 | 0.0037854117839999993 | 20835.5323731296 | 1376174.095079883 | 287.9821353333815 | 16.73643223844981 | 328873.27899784845 | 411099.53101342137 | 0.0
-0.08990000001666666 | -36957.84784495824 | 0.06326438781752873 | 0.0037854117839999993 | 20798.574525284643 | 1373401.5373179803 | 287.81432046081954 | 16.71268317093841 | 328756.433797688 | 410933.63558337325 | 0.001
-0.08980000013333331 | -36901.84053017806 | 0.06317458781739539 | 0.0037854117839999993 | 20761.672684754463 | 1370633.780759256 | 287.64655552894595 | 16.688960520601423 | 328639.6223868618 | 410767.79202737083 | 0.002
-0.08970000044999979 | -36845.87112970059 | 0.06308488781694539 | 0.0037854117839999993 | 20724.826813624764 | 1367870.8208134528 | 287.4788406846209 | 16.66526428738602 | 328522.8448651979 | 410602.0004804648 | 0.003
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

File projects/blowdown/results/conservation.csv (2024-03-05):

conservation_mdot [kg/s] | conservation_tank.mass [kg] | conservation_tank.volume [m^3] | conservation_tank.inenergy [J] | conservation_tank.pressure [Pa] | conservation_tank.temperature [degK] | conservation_tank.density [kg/m^3] | conservation_tank.sp_inenergy [J/kg] | conservation_tank.sp_enthalpy [J/kg] | time [s]
-0.0927179233146152 | 0.30755154796239087 | 0.0037854117839999993 | 61137.15441171456 | 6894757.293166357 | 288.1499999999284 | 81.24652363115032 | 198786.69061093705 | 283648.87283148954 | 0.0
-0.0927179233146152 | 0.30745883003907626 | 0.0037854117839999993 | 61110.8550772751 | 6891563.024381078 | 288.1105640409479 | 81.22203014705792 | 198761.09939502552 | 283609.54521582293 | 0.001
-0.09268129206945266 | 0.3073661487470068 | 0.0037854117839999993 | 61084.56977818126 | 6888370.654888592 | 288.0711385660284 | 81.19754633991673 | 198735.5147181806 | 283570.22913256206 | 0.002
-0.09264467992359966 | 0.3072735040670832 | 0.0037854117839999993 | 61058.29850506742 | 6885180.1832438335 | 288.03172357032844 | 81.17307220468125 | 198709.93657734094 | 283530.92457554466 | 0.003
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

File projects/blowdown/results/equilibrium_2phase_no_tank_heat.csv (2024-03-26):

volume [m^3] | pressure [Pa] | temp [degK] | liq_sp_intenergy [J/kg] | liquid_sat_density [kg/m^3] | vapor_sat_sp_inenergy [J/kg] | vapor_sat_density [kg/m^3] | x [-] | total_mass [kg] | total_inenergy [J] | total_mdot [kg/s] | total_inenergy_dot [J/s] | time [s]
0.008963947725436136 | 4777000.0 | 290.6947123517793 | 201746.46885608768 | 803.2175354580938 | 354347.54101512406 | 145.62671531354366 | 0.0 | 7.2 | 1452574.5757638314 | 0.0 | 0.0 | 0.0
0.008963947725436136 | 4776848.86057806 | 290.69333596064183 | 201743.0517332713 | 803.227329057175 | 354348.5674834507 | 145.62017644125197 | 1.944653682643158e-05 | 7.199455895618005 | 1452461.5686575877 | -0.5441043819954824 | -113007.10624370186 | 0.001
0.008963947725436136 | 4776697.727681927 | 290.69195959605497 | 201739.63663483903 | 803.2371166766447 | 354349.59326090204 | 145.6136417169088 | 3.888016094873497e-05 | 7.1989118113532875 | 1452348.5677295632 | -0.544084264717199 | -113000.92802463677 | 0.002
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

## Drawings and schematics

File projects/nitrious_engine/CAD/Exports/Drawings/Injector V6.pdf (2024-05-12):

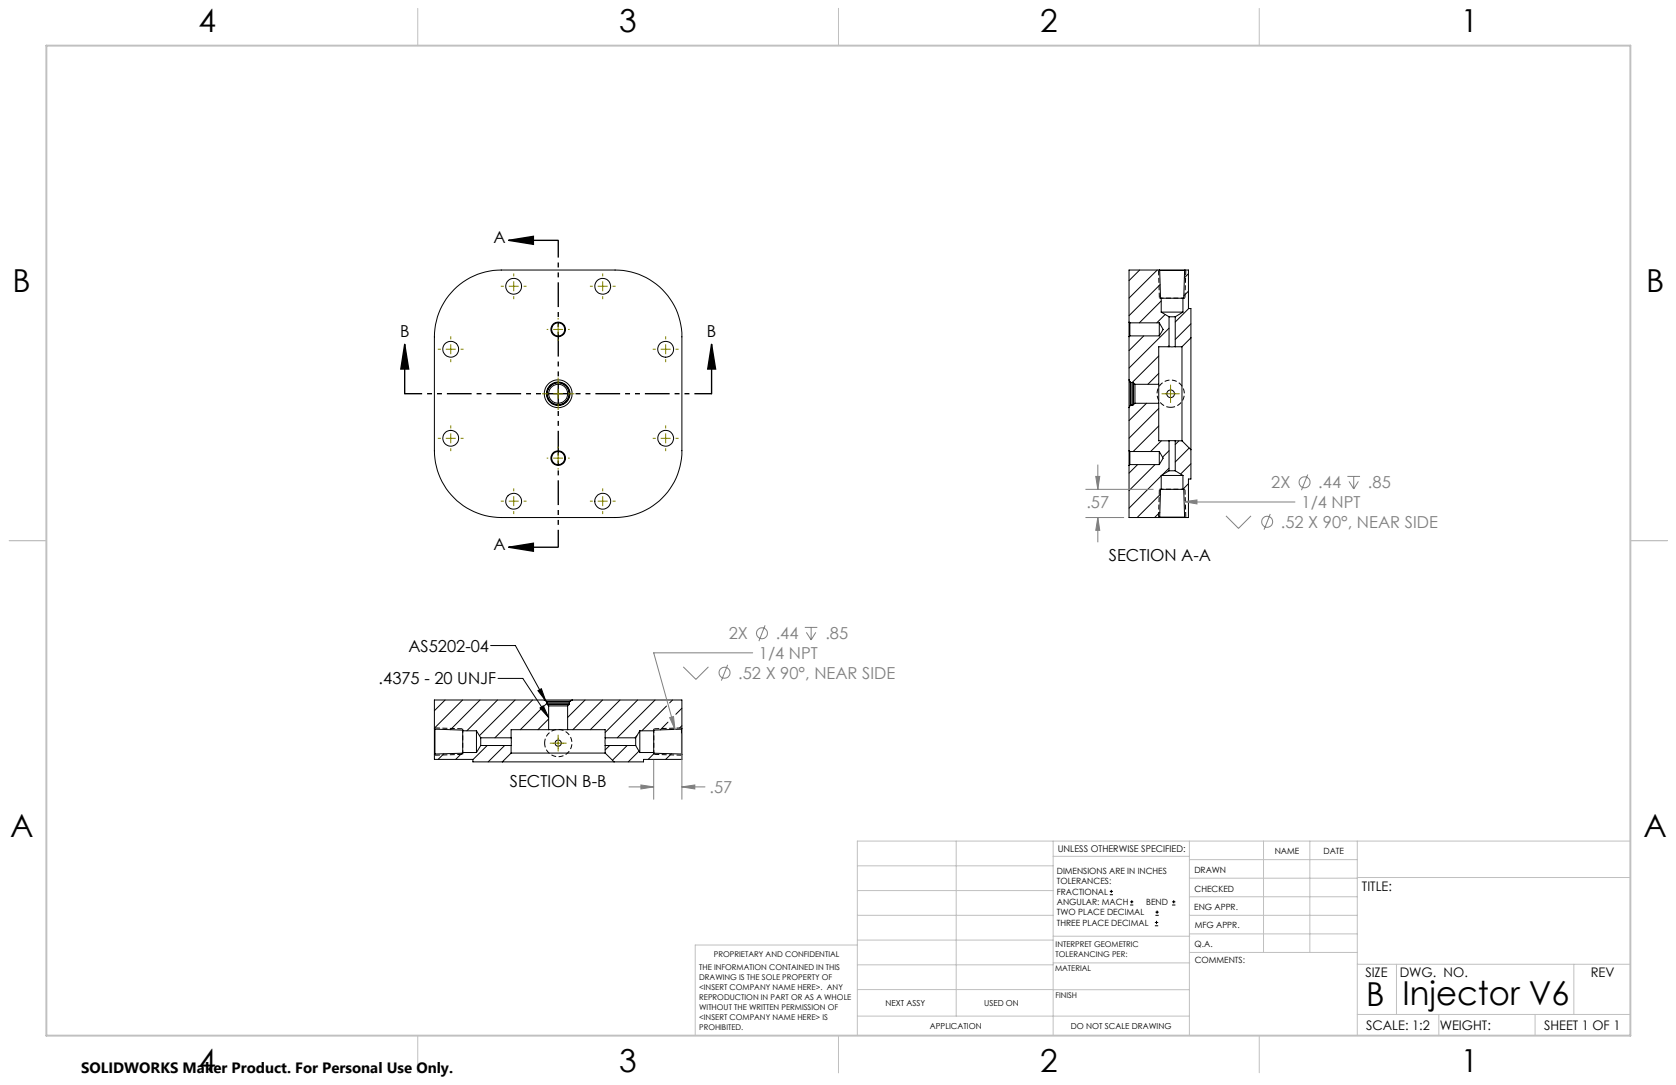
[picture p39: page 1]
1/4 NPT .52 X 90°, NEAR SIDE; SECTION A-A; .57 SECTION B-B; .4375 - 20 UNJF

UNLESS OTHERWISE SPECIFIED: | | NAME | DATE
DIMENSIONS ARE IN INCHES TOLERANCES: FRACTIONAL ANGULAR: MACH BEND TWO PLACE DECIMAL THREE PLACE DECIMAL | DRAWN

CHECKED | | | TITLE:

ENG APPR.
MFG APPR.

INTERPRET GEOMETRIC TOLERANCING PER: | Q.A.
MATERIAL | | SIZE B | DWG. NO. Injector V6 | REV

PROPRIETARY AND CONFIDENTIAL
THE INFORMATION CONTAINED IN THIS
DRAWING IS THE SOLE PROPERTY OF
<INSERT COMPANY NAME HERE>. ANY
REPRODUCTION IN PART OR AS A WHOLE
WITHOUT THE WRITTEN PERMISSION OF
<INSERT COMPANY NAME HERE> IS
PROHIBITED.

NEXT ASSY | USED ON | FINISH

APPLICATION | DO NOT SCALE DRAWING | | SCALE: 1:2 | WEIGHT: | SHEET 1 OF 1

SOLIDWORKS Maker Product. For Personal Use Only.

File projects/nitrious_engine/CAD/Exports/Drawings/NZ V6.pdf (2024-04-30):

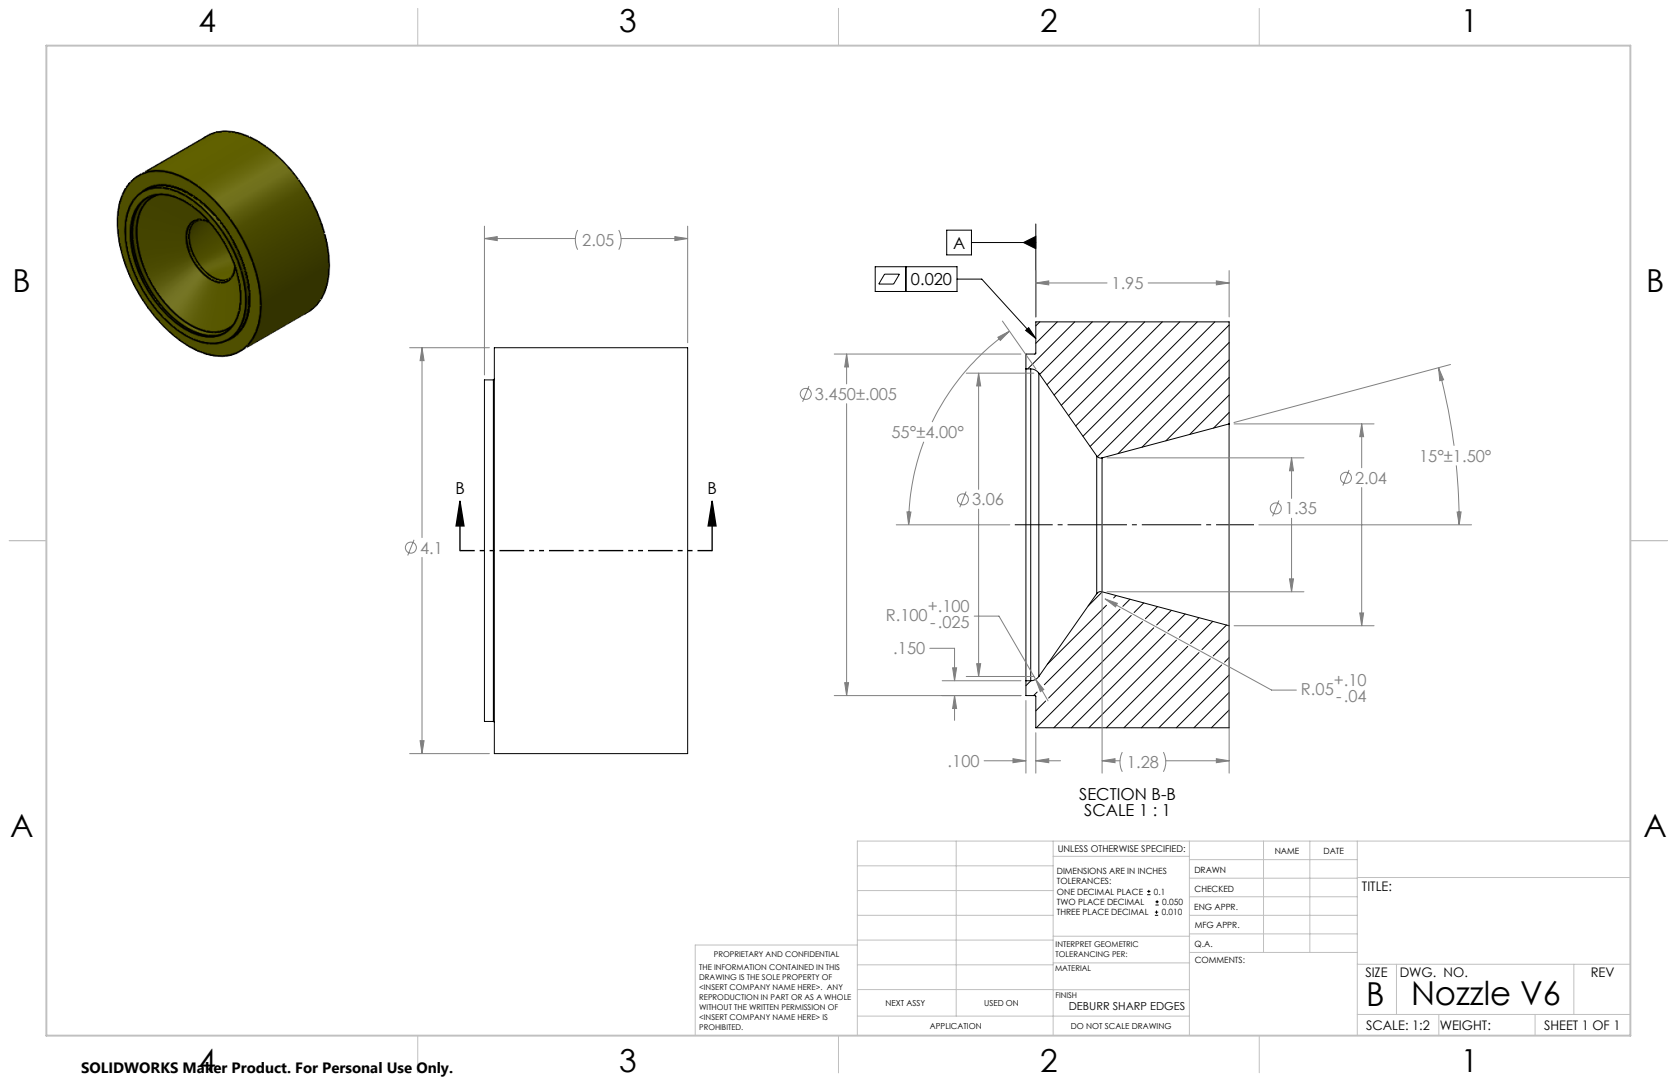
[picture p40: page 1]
SECTION B-B SCALE 1 : 1

UNLESS OTHERWISE SPECIFIED: | | NAME | DATE
DIMENSIONS ARE IN INCHES TOLERANCES: ONE DECIMAL PLACE 0.1 TWO PLACE DECIMAL 0.050 THREE PLACE DECIMAL 0.010 | DRAWN

CHECKED | | | TITLE:

ENG APPR.
MFG APPR.

INTERPRET GEOMETRIC TOLERANCING PER: | Q.A.
MATERIAL | | SIZE B | DWG. NO. Nozzle V6 | REV

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

NEXT ASSY | USED ON | FINISH DEBURR SHARP EDGES

APPLICATION | DO NOT SCALE DRAWING | | SCALE: 1:2 | WEIGHT: | SHEET 1 OF 1

SOLIDWORKS Maker Product. For Personal Use Only.

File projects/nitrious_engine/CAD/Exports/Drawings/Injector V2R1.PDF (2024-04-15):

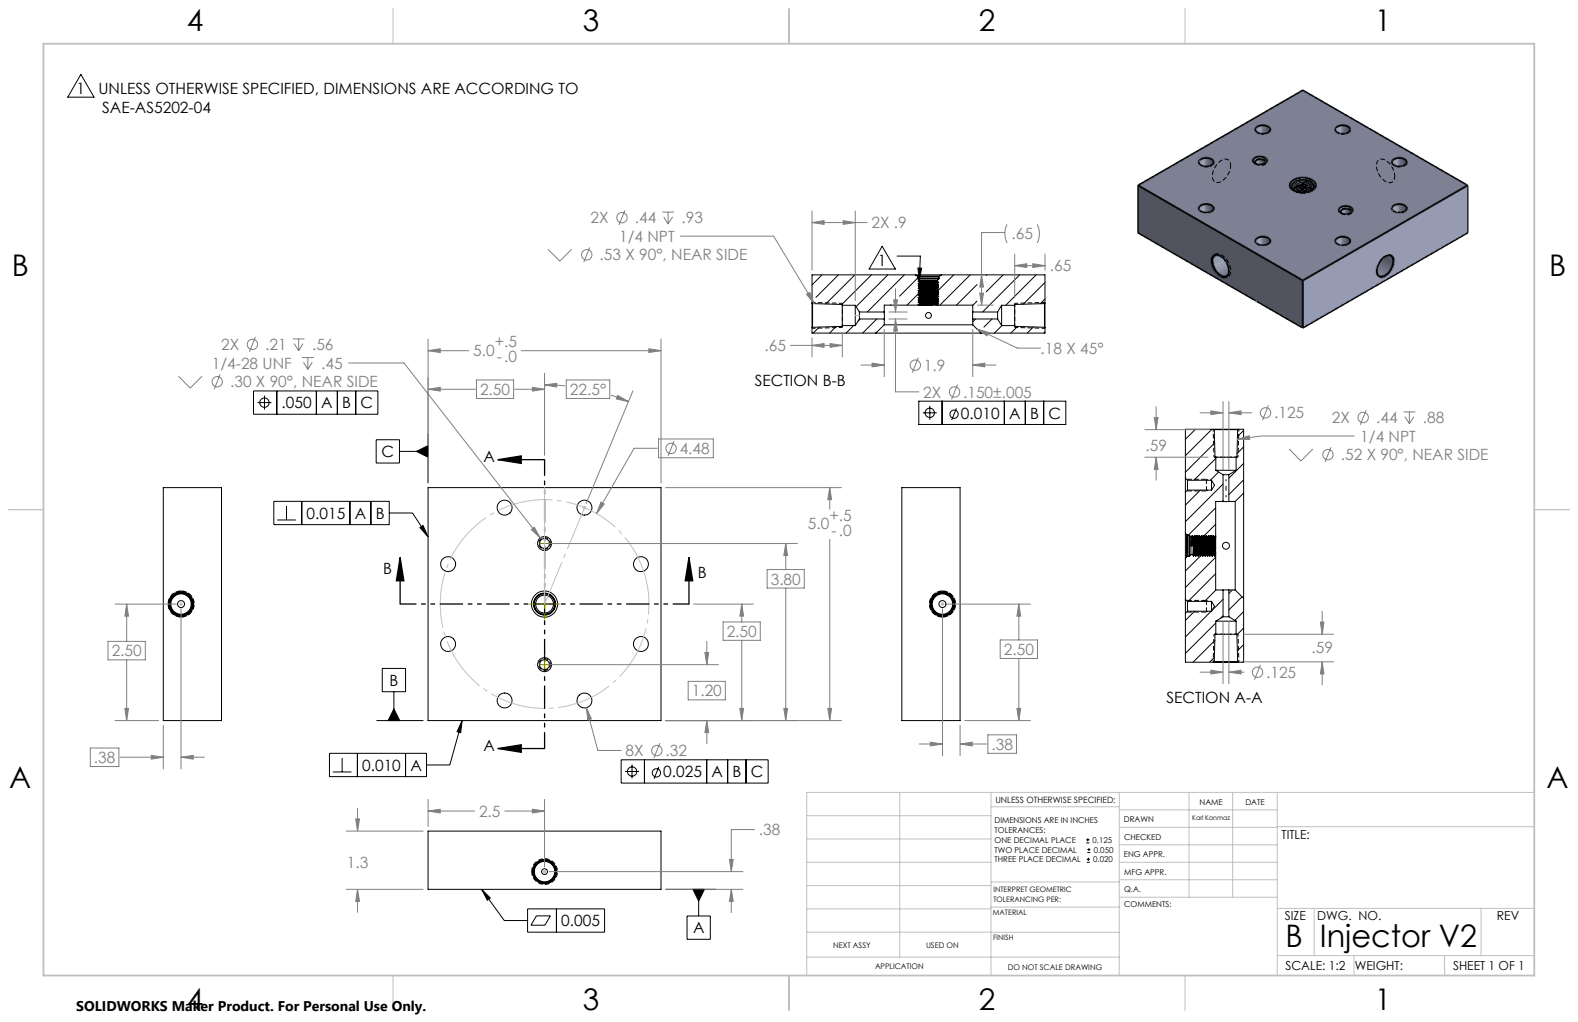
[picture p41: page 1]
1/4-28 UNF; .30 X 90°, NEAR SIDE; 1/4 NPT .52 X 90°, NEAR SIDE .59; SECTION A-A; 1/4 NPT .53 X 90°, NEAR SIDE; SECTION B-B

1 UNLESS OTHERWISE SPECIFIED, DIMENSIONS ARE ACCORDING TO
SAE-AS5202-04

UNLESS OTHERWISE SPECIFIED: | | NAME | DATE

DIMENSIONS ARE IN INCHES TOLERANCES: ONE DECIMAL PLACE 0.125 TWO PLACE DECIMAL 0.050 THREE PLACE DECIMAL 0.020 | DRAWN | Karl Kanmaz

CHECKED | | | TITLE:

ENG APPR.
MFG APPR.

INTERPRET GEOMETRIC TOLERANCING PER: | Q.A.
MATERIAL | | SIZE B | DWG. NO. Injector V2 | REV

NEXT ASSY | USED ON | FINISH

APPLICATION | DO NOT SCALE DRAWING | | SCALE: 1:2 | WEIGHT: | SHEET 1 OF 1

SOLIDWORKS Maker Product. For Personal Use Only.

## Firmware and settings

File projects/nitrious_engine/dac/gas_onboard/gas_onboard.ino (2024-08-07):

// Globals
const long datarate_ms = 3;
static long prev_ms = 0.0;

// Global Channels (in order)
static float time_s = -404.0;
static float sensor_voltage = -404.0;
static float ox_lc_a = -404.0;
static float ox_lc_b = -404.0;
static float ox_lc_c = -404.0;
static float ox_lc_d = -404.0;
static float fu_lc_a = -404.0;
static float fu_lc_b = -404.0;
static float fu_lc_c = -404.0;
static float fu_lc_d = -404.0;
static float ch_lc_a = -404.0;
static float ch_lc_b = -404.0;
static float ox_tc_093 = -404.0;
static float ox_tc_097 = -404.0;
static float fu_tc_056 = -404.0;
static float ch_stc_101_a = -404.0;
static float ch_stc_101_b = -404.0;
static float ch_stc_101_c = -404.0;
static float ox_pt_094 = -404.0;
static float ox_pt_098 = -404.0;
static float n2_pt_019 = -404.0;
static float ch_pt_100 = -404.0;

static bool is_recording = false;
static bool is_streaming = false;

// State machine
typedef enum{
  STATE_ERROR = 0,
  STATE_IDLE = 1
} state_options;
static state_options State;


void setup_try(){
  Serial.print("Using File: ");
  Serial.println(__FILE__);
  if(sd_setup() == 0) while(1); // <- get stuck here like a pro c++ coder
  if(instrumentation_setup() == 0) while(1);
}

void setup() {
  Serial.begin(9600);
  Serial.println("\nWelcome! Hopfully this works out for ya, lets walk through some setup");
  Serial.println("Would you like to continue this adventure? (y to continue)");
  delay(2000);

  while (1){
    if (Serial.available() > 0){
      String message = Serial.readString();
      if (message == "y"){
        Serial.println(":S okay then!");
        State = STATE_IDLE ;
        setup_try();
        break;
      }
    }
    delay(100);
  }
}
void loop() {
  switch (State){
    case STATE_IDLE:
        if (Serial.available() > 0) {
          String message = Serial.readString();
          user_inputs(message);
        };
      break;
    default:
      Serial.println("You have found a Poisen Arrow cause Joe Fucked up");
  };

  update_instrumentation();
  do_the_data();

  long ms = millis();
  long cur_dms = ms - prev_ms;
  time_s = ms / 1000.0;
  if (cur_dms > datarate_ms){
    Serial.print("WARNING| data rate is being choked: ");
    Serial.println(cur_dms);
  }
  prev_ms = ms;
  // Limit loop cycle sample rate
  while (millis() - prev_ms < datarate_ms){};
}

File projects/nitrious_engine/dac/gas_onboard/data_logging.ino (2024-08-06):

#include <SdFat.h>
#include <SPI.h>
#define FILE_BASE_NAME "log-"

SdFat sd;
SdFile File;

// Use Teensy SDIO
#define SD_CONFIG  SdioConfig(FIFO_SDIO)

static String data_file_name;
static float relative_time_start_s;



// =================================================================================================
// Configure data, NOTE: This is pretty sketch as there no catch for length checks.... or ordering

const char header[] =
"run_time [s],"\
"time [s],"\
"state [-],"\
"Sensor Bus [Volts],"\
"OX-LC-A [lbf],"\
"OX-LC-B [lbf],"\
"OX-LC-C [lbf],"\
"OX-LC-D [lbf],"\
"FU-LC-A [lbf],"\
"FU-LC-B [lbf],"\
"FU-LC-C [lbf],"\
"FU-LC-D [lbf],"\
"CH-LC-A [lbf],"\
"CH-LC-B [lbf],"\
"OX-TC-093 [degF],"\
"OX-TC-097 [degF],"\
"FC-TC-056 [degF],"\
"CH-STC-101-A [degF],"\
"CH-STC-101-B [degF],"\
"CH-STC-101-C [degF],"\
"OX-PT-094 [psig],"\
"OX-PT-098 [psig],"\
"N2-PT-019 [psig],"\
"CH-PT-100 [psig]";

const int places = 4;

void file_data(float value){
  File.print(value, places);
  File.print(",");
}

void write_data(){

  float relative_time_s = time_s - relative_time_start_s;

  file_data(time_s);
  file_data(relative_time_s);
  file_data(State);
  file_data(sensor_voltage);
  file_data(ox_lc_a);
  file_data(ox_lc_b);
  file_data(ox_lc_c);
  file_data(ox_lc_d);
  file_data(fu_lc_a);
  file_data(fu_lc_b);
  file_data(fu_lc_c);
  file_data(fu_lc_d);
  file_data(ch_lc_a);
  file_data(ch_lc_b);
  file_data(ox_tc_093);
  file_data(ox_tc_097);
  file_data(fu_tc_056);
  file_data(ch_stc_101_a);
  file_data(ch_stc_101_b);
  file_data(ch_stc_101_c);
  file_data(ox_pt_094);
  file_data(ox_pt_098);
  file_data(n2_pt_019);
  File.println(ch_pt_100);
}

void serial_print_data(){
  Serial.print(sensor_voltage);
  Serial.print(",");
  Serial.print(ox_lc_a + ox_lc_b + ox_lc_c + ox_lc_d);
  Serial.print(",");
  Serial.print(fu_lc_a + fu_lc_b + fu_lc_c + fu_lc_d);
  Serial.print(",");
  Serial.print(ox_tc_093);
  Serial.print(",");
  Serial.print(ox_tc_097);
  Serial.print(",");
  Serial.print(fu_tc_056);
  Serial.print(",");
  Serial.print(ch_stc_101_a);
  Serial.print(",");
  Serial.print(ch_stc_101_b);
  Serial.print(",");
  Serial.print(ch_stc_101_c);
  Serial.print(",");
  Serial.print(ox_pt_094,places);
  Serial.print(",");
  Serial.print(ox_pt_098,places);
  Serial.print(",");
  Serial.print(n2_pt_019,places);
  Serial.print(",");
  Serial.println(ch_pt_100,places);
}

// =================================================================================================
int sd_setup() {
  Serial.println("__ SD Setup __");
 // Initialize the SD.
  if (!sd.begin(SD_CONFIG)) {
    Serial.println("ERROR| Failed to configure SD, check if its in the thingy");
    return 0;
  }
  Serial.println("SD Setup complete");
  return 1;
}

void print_header(){
  Serial.println(header);
}

void writeHeader() {
  File.println(header);
  File.sync();
}

void close_data(){
  File.close();
  Serial.println("Data has been saved");
}

void do_the_data() {
  if (is_streaming){
    serial_print_data();
  }
  if (is_recording){
    write_data();
  }
}



int init_data_file(){
  // Shitty copy pasta code to itterate the next file name
  const uint8_t BASE_NAME_SIZE = sizeof(FILE_BASE_NAME) - 1;
  char file_name[13] = FILE_BASE_NAME "00.csv";
  if (BASE_NAME_SIZE > 6) {
    Serial.println("ERROR| FILE_BASE_NAME too long");
  }
  while (sd.exists(file_name)) {
    if (file_name[BASE_NAME_SIZE + 1] != "9") {
      file_name[BASE_NAME_SIZE + 1]++;
    } else if (file_name[BASE_NAME_SIZE] != "9") {
      file_name[BASE_NAME_SIZE + 1] = "0";
      file_name[BASE_NAME_SIZE]++;
    } else {
      Serial.println("ERROR| Can't create file name");
    }
  }

// Open or create file - truncate existing file.
  if (!File.open(file_name, O_RDWR | O_CREAT | O_TRUNC)) {
    Serial.println("ERROR| Fail to open file");
    return 0;
  }

  Serial.print(F("File Name: "));
  Serial.println(file_name);

  // Write data header.
  writeHeader();
  relative_time_start_s = time_s;

  return 1;
}

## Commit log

2024-01-26 working runtime failed fluidslookups!
    [test.csv]
2024-01-27 better working versio with some bug fixes (runtime errors, lookup type checking ect
    [test.csv]
2024-01-27 working blowdown example with graphs, results and a progress bar when recording
    [conservation.csv, isenthalpic.csv, isentropic.csv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]
2024-02-04 namespace fixed
    [isentropic.csv]
2024-02-05 liquid start
    [conservation.csv, isenthalpic.csv, isentropic.csv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]
2024-02-11 pretty printing dicitonaries like a silly gose" gi
2024-02-25 easier than a rebase
    [real.csv]
2024-02-25 failed unchoked still
    [ideal.csv]
2024-03-05 running all projects
    [conservation.csv, isenthalpic.csv, isentropic.csv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]
2024-03-10 added some rust code to make the heat transfer far easier
2024-03-25 hem, dryer ect
    [equilibrium_2phase_no_tank_heat.csv]
2024-04-04 added cylinder stress and b313
2024-04-07 add diagrams
    [BOM.ods]
2024-04-12 bom update 2
    [BOM.ods]
2024-04-13 pressure ladder update
2024-04-30 updated stuff
    [12x12_Plate.SLDPRT, 1491N146_Threaded Brass Pipe Fitting for Drinking Water.SLDPRT, 1491N244_Threaded Brass Pipe Fitting for Drinking Water.SLDPRT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]
2024-04-30 updated exports folder
    [Injector V2.SLDDRW, Injector V2.SLDPRT, Injector V2.STEP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]
2024-05-04 Added CAD parts and assemblies from local PC to git folder
    [50715K163_37 Degree Flared Fitting for Stainless Steel Tubing.SLDPRT, 98804A487_18-8 Stainless Steel Threaded Rod.SLDPRT, TCA V10.SLDPRT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]
2024-05-04 updated pressure ladder to reflect different length values, relative roughness. Also changed fuel orifice size lowering the injector DP to meet 200 psi tank press
    [TCA V10.SLDPRT]
2024-05-05 added tank
    [20-2020-400-cl.SLDPRT, 40-4040-500-cl.SLDPRT, 4040_20mm_slot_corner.SLDPRT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]
2024-05-05 added parts and brackets
    [20-2020-400-cl.SLDPRT, 40-4040-500-cl.SLDPRT, 4040_20mm_slot_corner.SLDPRT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]
2024-05-05 removed plots from global scope, and updated paths in pressure ladder
2024-05-06 ladder with new roughness and CAD work
    [TCA V10.SLDPRT]
2024-05-12 CAD stuff and excel sheet
    [GasLighter Engine V1.xlsx, Injector V6 (ProtoQuote).SLDPRT, Injector V6.SLDDRW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]
2024-05-12 Sheet update
    [GasLighter Engine V1.xlsx]
2024-05-21 got seom results
    [BOM.ods, GasLighter Engine V1.xlsx, ipa_pressure_ladder.csv]
2024-05-30 I beam test stand
    [2020 Framing, 1 ft.SLDPRT, 2020 Framing, 3 inch (Cut).SLDPRT, 2020 Framing, 6 inch.SLDPRT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]
2024-06-09 ppt changes
    [Nozzle V11.SLDPRT, TCA V18.SLDPRT]
2024-07-14 post process and first pass logging
    [log-13.csv, log-14.csv]
2024-07-16 updated logging
    [log-0001.csv, log-13.csv, log-14.csv]
2024-07-27 updated tcs and adc
    [log-06.csv, log-09.csv, log-10.csv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]
2024-07-30 added calculator for instrumentation
    [log-12.csv]
2024-08-03 updated daqarittots
    [sensor_calcs.ods]
2024-08-03 sensor calcs
    [sensor_calcs.ods]
2024-08-06 500hz going strong as hell
    [log-02.csv, log-04.csv, log-05.csv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]
